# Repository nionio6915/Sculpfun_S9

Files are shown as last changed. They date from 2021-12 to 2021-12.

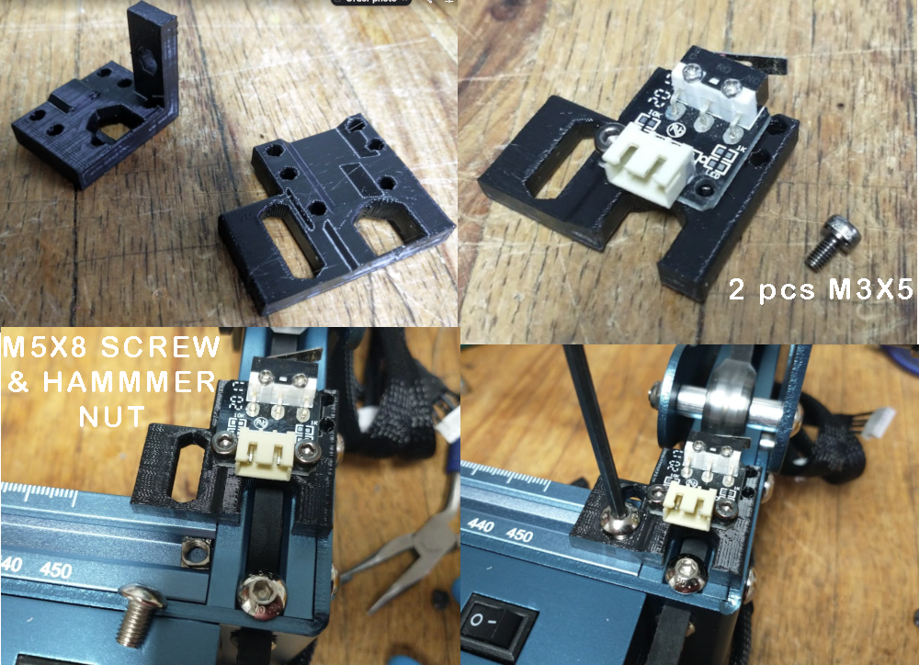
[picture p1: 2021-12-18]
images/Y_Assy.png

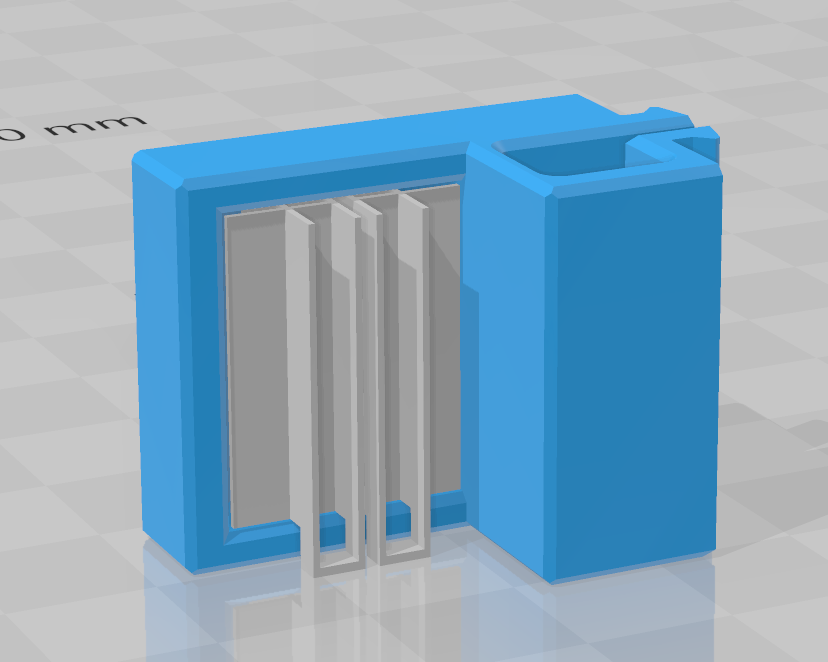
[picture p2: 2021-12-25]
images/CylinderHolderSTL.png

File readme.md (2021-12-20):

Adding endstops / homing switches to Sculpfun S9 Laser Engraver
12/19/2021 This is a continual work in progress. Information may change and be revised without notice. As with anythithing you find  on the interwebs, your mileage may vary and with altering any electronic components, there are inherent risks.
  
Why: repeatabilty and consistency. For my use, I need a consistent and repratable start posistion for my work. I have a stop/fence on the spoils baord and I justify and clamp the work to it. 

If you are just tossing some random thing under the laser and etching pretty pictures, this is prpbably not going to matter to you. 

1. Print the endstop brackets. There are 2 versions for each of the X & Y axis. One is for reprap 3-wire types, and one for miniature and sub-miniature SPDT snap action switches.  
Only the non-LED illuminated Reprap endstop switch will work. See https://reprap.org/wiki/Mechanical_Endstop for descriptions.   
See this page for wiring limit switchs to 2-axis system with grbl.  
https://github.com/gnea/grbl/wiki/Two-Axis-System-Considerations and  
https://github.com/gnea/grbl/wiki/Wiring-Limit-Switches  

2. Mount the brackets. Each bracket requires an M5x8 screw and a 'hammernut' to twist into the extrusion channel.

3. Wire the endstops to the controller. Depending on where you mount the endstops, you will need 1m or 2m of 3-wire cable and connectors.  The DLC board uses 3-pin JST XH connectors.

4. Upload the updated firmware that has the homing function compiled into it. 
Using either LAsergrbl or Lightburn, flash the firmware to the controller. 

5. Configure grbl to recognize the switches and the homing direction. 

From the main grbl configuration page- 
https://github.com/gnea/grbl/wiki/Grbl-v1.1-Configuration

pay particular attention to the secion the invert mask and corresponding table.

https://github.com/gnea/grbl/wiki/Grbl-v1.1-Configuration#2--step-port-invert-mask

These are the stock grbl EEPROM parameters for an S9 with DLC version 1.0 controller, grbl version 1.1f as shipped, and with the updates after flashing the .hex file to 1.1h. 

| Orignal grbl 1.1f settings | | | Updated grbl 1.1h settings | | | | |
|---|---|---|---|---|---|---|---|
| Parameter | | Original Value | Updated Value | Status  | Units | Descriptions | Comment |
| $0 | = | 10 | 10 | | microseconds | Step pulse time | |
| $1 | = | 25 | 25 | | milliseconds | Step idle delay | |
| $2 | = | 0 | 0 | | mask | Step pulse invert | https://github.com/gnea/grbl/wiki/Grbl-v1.1-Configuration#2--step-port-invert-mask |
| $3 | = | 0 | 0 | | mask | Step direction invert | |
| $4 | = | 0 | 0 | | boolean | Invert step enable pin | |
| $5 | = | 0 | 0 | | boolean | Invert limit pins | |
| $6 | = | 0 | 0 | | boolean | Invert probe pin | |
| $10 | = | 1 | 1 | | mask | Status report options | |
| $11 | = | 0.01 | 0.01 | | mm | Junction deviation | |
| $12 | = | 0.002 | 0.002 | | mm | Arc tolerance | |
| $13 | = | 0 | 0 | | boolean | Report in inches | |
| $20 | = | 0 | 1 | Changed | boolean | Soft limits enable | Safey feature-imposes the movement limits defined by $130 - $132 |
| $21 | = | 0 | 1 | Changed | boolean | Hard limits enable | Safety feature- use the switches to halt motion when triggered. |
| $22 | = | 0 | 1 | Changed | boolean | Homing cycle enable | Homing feature - result is the machine knows precise and knownposition |
| $23 | = | 0 | 3 | Changed | mask | Homing direction invert | Binary number to direct homing directions Invert X,Invert Y, Z normal |
| $24 | = | 25 | 200 | Changed | mm/min | Homing locate feed rate | Homing slow moves speeds. |
| $25 | = | 500 | 3000 | Changed | mm/min | Homing search seek rate | Homing fast moves speeds. |
| $26 | = | 250 | 250 | | milliseconds | Homing switch debounce delay | |
| $27 | = | 1 | 3 | Changed | mm | Homing switch pull-off distance | Retract distance to reset switch after homing. |
| $30 | = | 1000 | 1000 | | RPM | Maximum spindle speed | |
| $31 | = | 0 | 0 | | RPM | Minimum spindle speed | |
| $32 | = | 1 | 1 | | boolean | Laser-mode enable | |
| $100 | = | 80 | 80 | | steps/mm | X-axis travel resolution | |
| $101 | = | 80 | 80 | | steps/mm | Y-axis travel resolution | |
| $102 | = | 250 | 250 | | steps/mm | Z-axis travel resolution | |
| $110 | = | 6000 | 6000 | | mm/min | X-axis maximum rate | |
| $111 | = | 6000 | 6000 | | mm/min | Y-axis maximum rate | |
| $112 | = | 1000 | 1000 | | mm/min | Z-axis maximum rate | |
| $120 | = | 1000 | 1000 | | mm/sec^2 | X-axis acceleration | |
| $121 | = | 1000 | 1000 | | mm/sec^2 | Y-axis acceleration | |
| $122 | = | 10 | 1000 | Changed | mm/sec^2 | Z-axis acceleration | |
| $130 | = | 410 | 410 | | mm | X-axis maximum travel | |
| $131 | = | 400 | 400 | | mm | Y-axis maximum travel | |
| $132 | = | 200 | 200 | | mm | Z-axis maximum travel | |

This is the invert mask from the grbl firmware. grbl default moves are to the MAX directions on each axis. Any direction change casued by the machine configuration needs to be set in the firmware with one of the following masks by setting the integer value in the table.  

| Setting Value | Mask | Invert X | Invert Y | Invert Z |
|---|---|---|---|---|
| 0 | 00000000 | N | N | N |
| 1 | 00000001 | Y | N | N |
| 2 | 00000010 | N | Y | N |
| 3 | 00000011 | Y | Y | N |
| 4 | 00000100 | N | N | Y |
| 5 | 00000101 | Y | N | Y |
| 6 | 00000110 | N | Y | Y |
| 7 | 00000111 | Y | Y | Y |

The hooming switches in the Sculpfun instructions were are Xmin & Ymin, so the configration mask was "3"- 
  X Invert  Y Invert   Z Normal
Homing switches in this deployment are located at Xmax & Ymin so we must adjust the values accordindly to "2"
  X Normal  Y Invert  Z Normal 

6. Websites with good grbl info

https://github.com/gnea/grbl/wiki

https://diymachining.com/grbl-update/

https://lightburnsoftware.github.io/NewDocs/CommonGrblSetups.html

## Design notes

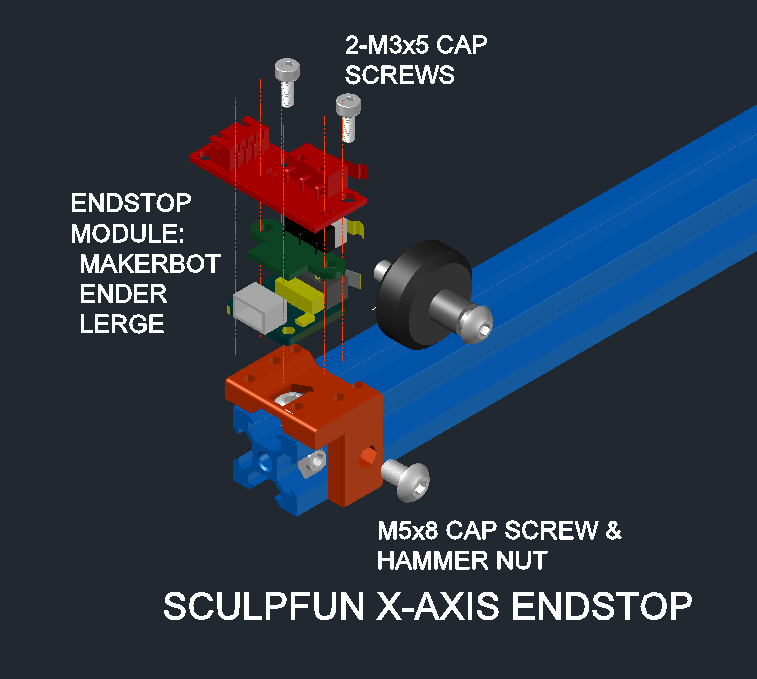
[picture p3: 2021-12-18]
images/X_Endstop.png

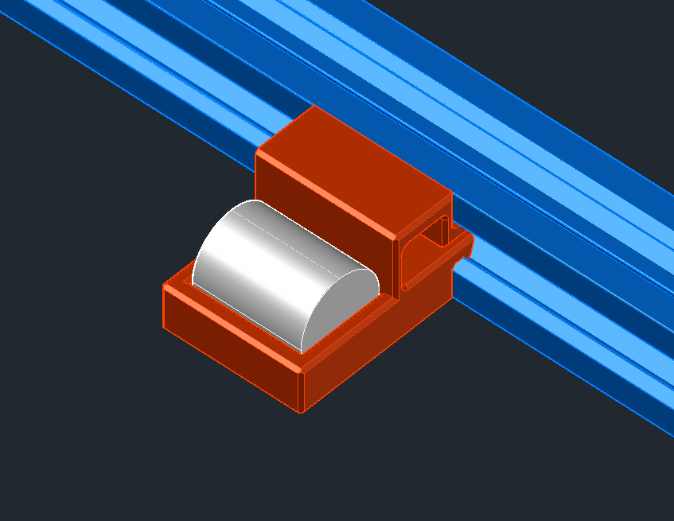
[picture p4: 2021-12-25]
images/CylinderHolder.png

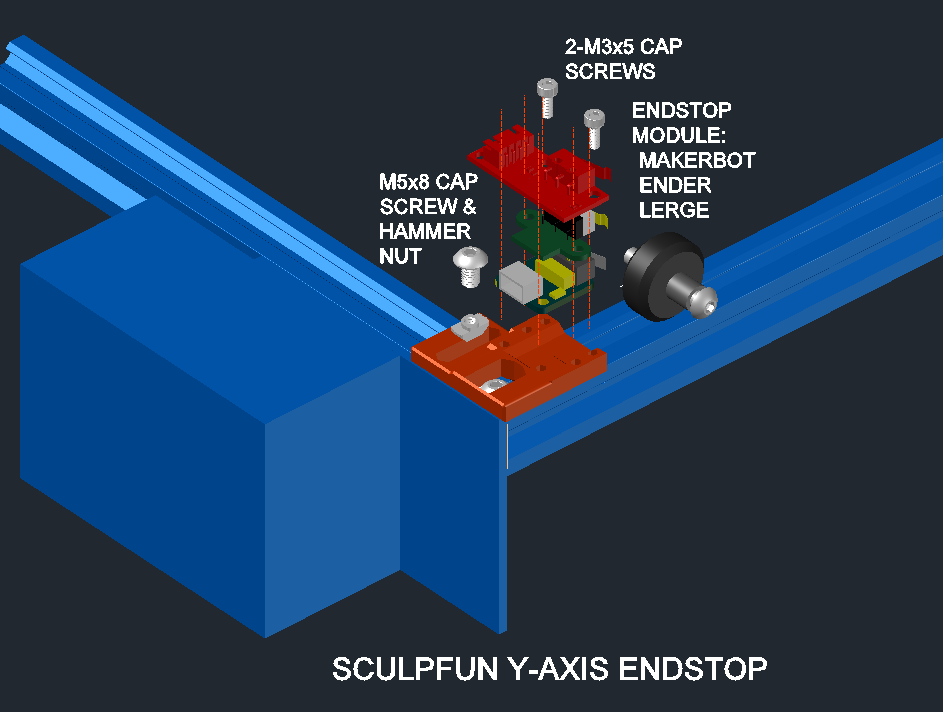
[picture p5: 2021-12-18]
images/Y_Endstop.png

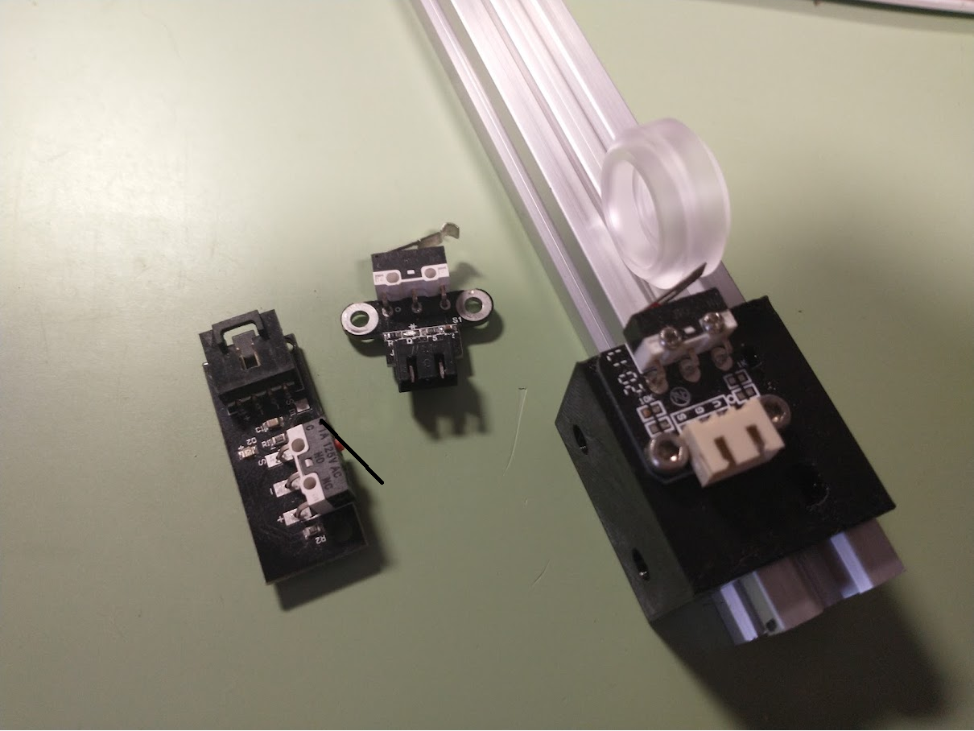
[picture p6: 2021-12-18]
images/Untitled.png

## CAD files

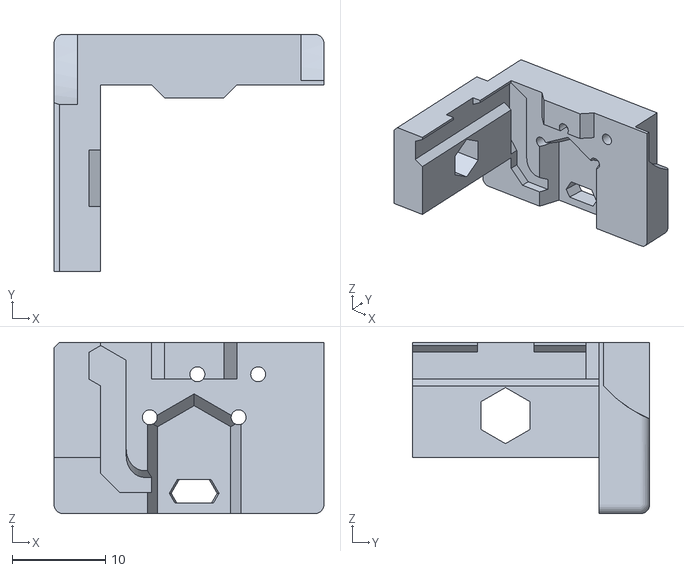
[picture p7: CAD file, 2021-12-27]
NewXStopsIIISPDT.stl
28.9 x 25.4 x 18.3

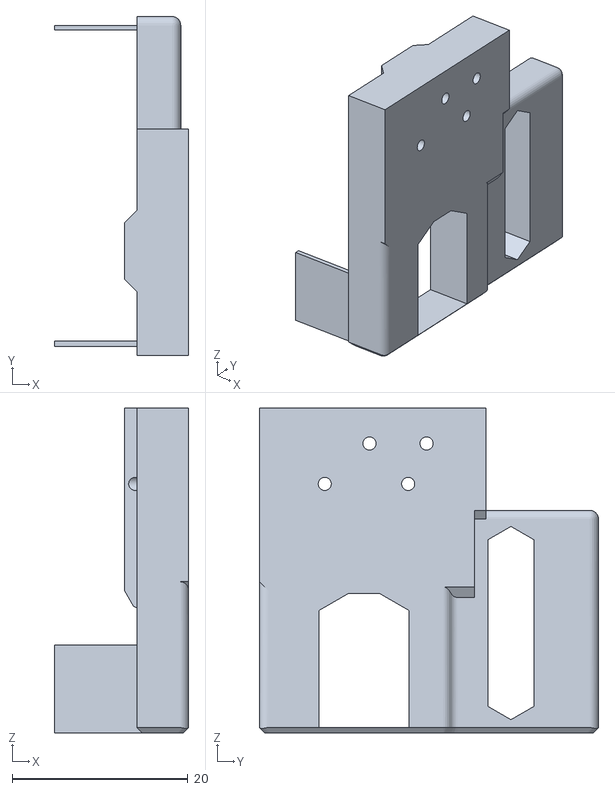
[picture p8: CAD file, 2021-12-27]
stls/Y_SPDT_Endstop_Right.stl
15.3 x 38.6 x 37.0

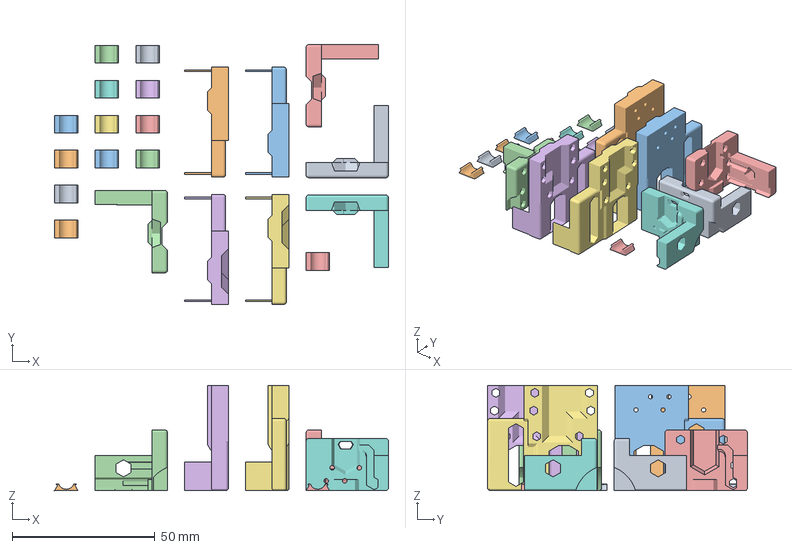
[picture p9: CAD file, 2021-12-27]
stls/ProovingPArts.3mf
117.1 x 91.1 x 37.0 mm
VSlot_Wire_Retainers.stl
Y-EndstopAdapter_Left.stl
Y-EndstopAdapter_Right.stl
X_SPDT_Endstop_FL.stl
X_SPDT_Endstop_FR.stl
Y_SPDT_Endstop_Left.stl
Y_SPDT_Endstop_Right.stl
X_Endstop_FR.stl
X_Endstop_FL.stl

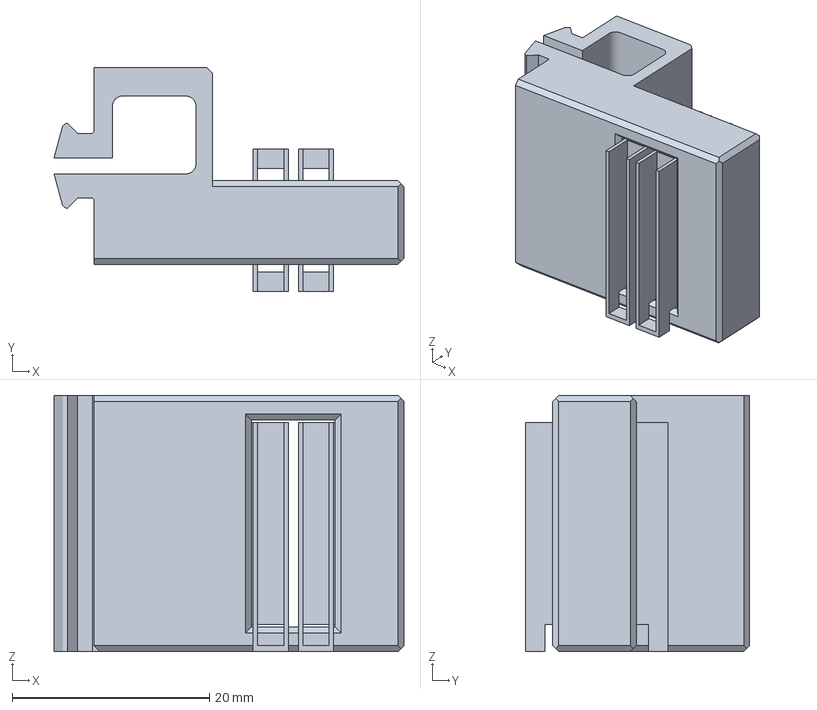
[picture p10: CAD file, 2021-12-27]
stls/SpacerCylinderHolder4.3mf
35.5 x 22.8 x 26.0 mm

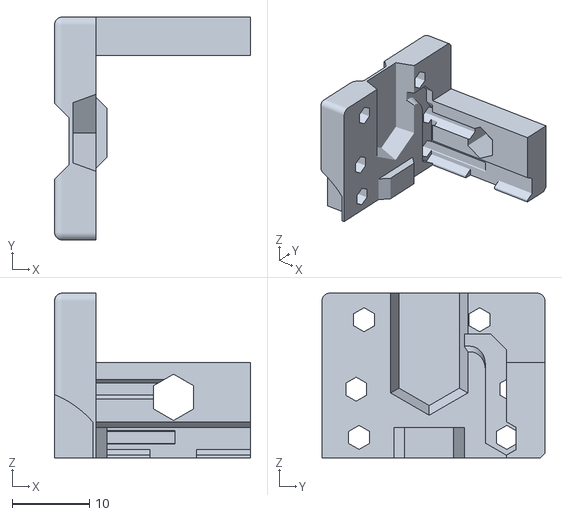
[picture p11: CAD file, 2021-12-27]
stls/X_Endstop_FL.stl
25.4 x 28.9 x 21.3

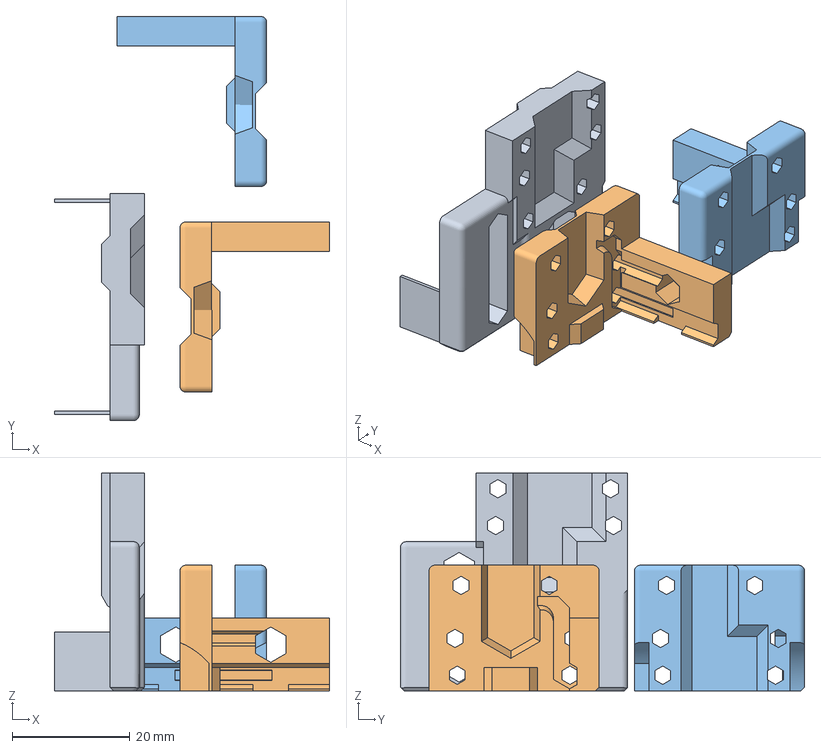
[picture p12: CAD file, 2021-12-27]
stls/X_Endstop_FR.3mf
46.7 x 68.6 x 37.0 mm
Y-EndstopAdapter_Right.stl
X_Endstop_FL.stl
X_Endstop_FR.stl

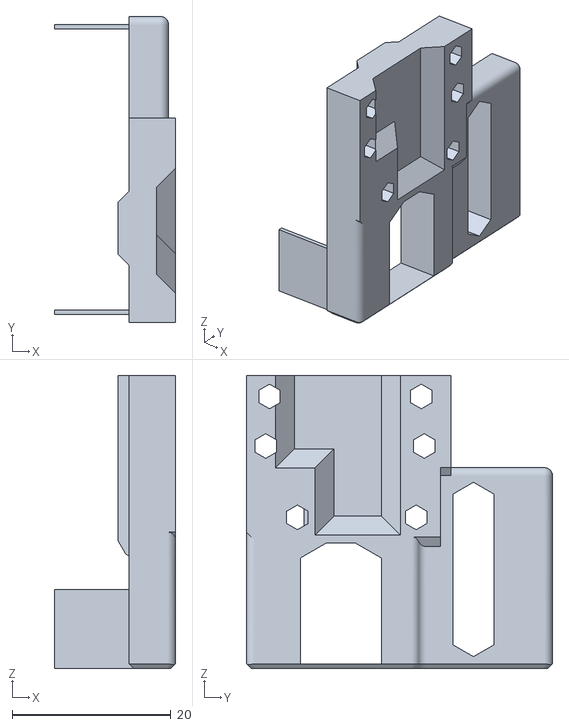
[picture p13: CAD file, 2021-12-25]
stls/Y-EndstopAdapter_Left.stl
15.3 x 38.6 x 37.0

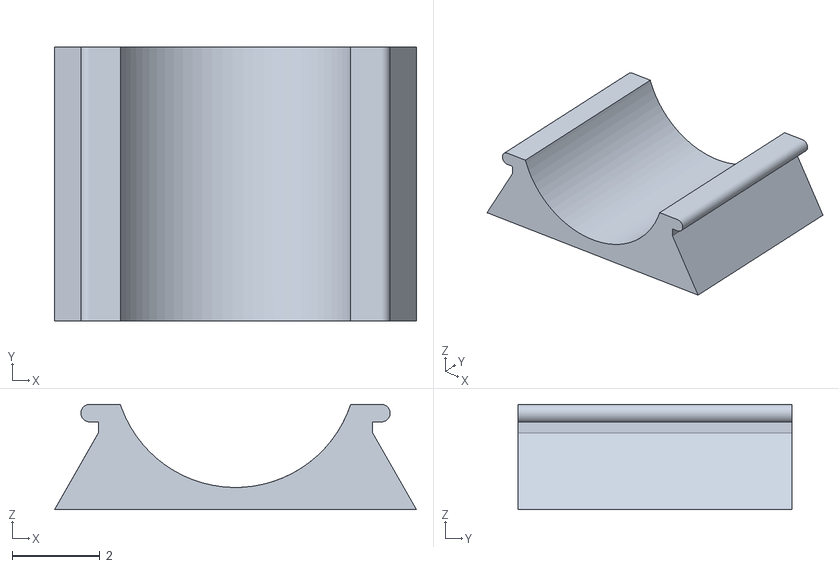
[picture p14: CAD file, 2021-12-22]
stls/VSlot_Wire_Retainers.stl
8.25 x 6.25 x 2.40

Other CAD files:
NewXStopsIVSPDT.stl
stls/Y_SPDT_Endstop_Left.stl
NewXStopsISPDT.stl
stls/X_SPDT_Endstop_BR.stl
stls/X_SPDT_Endstop_BL.stl
stls/X_SPDT_Endstop_FR.stl
stls/X_SPDT_Endstop_FL.stl
stls/Y-EndstopAdapter_Right.stl
stls/Cylinder_Holder.stl
stls/X_Endstop_FR.stl

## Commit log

2021-12-18 1ST Upload
    [XEndstopAdapterV5.stl, YEndstopAdapterV5.stl]
2021-12-19 Added readme.md
    [EndstopAdapter_20mmSPDT.stl, EndstopAdapter_Y_20mmSPDT.stl, X-EndstopAdapter.stl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]
2021-12-20 1stattemptat table
    [EndstopAdapter_20mmSPDT.stl, EndstopAdapter_X_20mmSPDT.stl, EndstopAdapter_Y_20mmSPDT.stl]
2021-12-20 tweaks to widths
    [EndstopAdapter_X_20mmSPDTV5.stl, EndstopAdapter_Y_20mmSPDT_Left.stl, EndstopAdapter_Y_20mmSPDT_Right.stl]
2021-12-22 Added V-Slot wire keeprs
    [EndstopAdapter_X_20mmSPDTV5.stl, VSlot_5mm.stl]
2021-12-25 cylinder holder
    [Cylinder_Holder.stl, EndstopAdapter_X_20mm_SPDT_Left.stl, EndstopAdapter_X_3Wire_Left.stl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]
2021-12-27 file cleanups
    [EndstopAdapter_X_20mmSPDT.stl, EndstopAdapter_X_20mmSPDTV5.stl, EndstopAdapter_X_20mm_SPDT_Left.stl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]
